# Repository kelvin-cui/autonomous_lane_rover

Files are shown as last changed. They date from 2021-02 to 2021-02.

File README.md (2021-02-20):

# autonomous lane following rover
152375054-496836404648972-4190929028758680099-n

Autonomous lane-following rover using openCV to identify and predict lane positions, and KP feedback loop for movement control, and ROS as a robotics framework to combine different modules together. The image processing was done on a Raspberry Pi 4B, which sends the appropriate motor commands to an Arduino Nano, which then sends the commands to stepper motors controlling a differential drive.

## objective
The lane-following rover was designed to follow a lane marked by duct tape, as a proof of concept for future projects. I wanted to create a project utilizing ROS and feedback control schemes, which I learned in class. OpenCV was something that I wanted to learn on my own, applying it for lane detection for this project. Putting these together, I wanted to create a robot that would follow a track with challenging features, such a chicanes and decreasing radius turns. 

rover

## software design:

### lane detection:
The lane detection was done utilizing OpenCV, in the camera.py module. When a ROS image is received, the module first converts it to an OpenCV image. The image is then masked to only detect a certain distance away from the rover, ignoring objects in the distant background. It then finds the canny edges, which are then grouped into lanes using hierarchical clustering, based on each points relative euclidian distance. Then, the cluster of points is fitted to a quadratic equation, which predicts the lane position near the center of the robot. It then finds the middle of the lane in terms of pixels as well as phi_avg, the angle the lanes are relative to the robot. 

Lane Detection:

*Left: The white lines are the predicted lanes, green are the left and right lane x locations, and the red line represents the middle of both lanes, as well as the slope of the lane. Right : The Canny Edges detected after the mask is applied*

### movement:
x_avg and phi_avg are then used in a KP feedback loop. x_avg is centred at 0, ranging from -320pixels to +320pixels (the camera has a resolution of 640 pixels across). Similarly, phi_avg is centred at 0, ranging from -90degrees to 90degrees. Both are normalized to -1/+1, and then used in a proportional feedback loop to regulate the values to zero. The forward velocity is fixed at 0.07m/s, while the rotational velocity is controlled by this feedback loop, with tunable gains on the x_error and phi_error. This can all be found in move.py. Once the rotational velocity is determined, it's then sent to motor.py, which takes the linear and rotational velocities and calculates the rotational speed of each motor.

Lane Following:

### ros and optimization:
The different modules communicate using the ROS framework. The original camera image is published to the image_raw topic, which is subscribed to by the camera.py node. The camera node publishes to the x_avg and phi_avg topics with Float64 values, which is subscribed to by the move.py node. The Move node then publishes Twist messages, including the linear and rotational velocities, which are subscribed to by the motor.py node. The motor.py node communicates the motor commands over serial to the Arduino. 

I made use of two external ros packages - the usb_cam test package in order to quickly publish images from the Pi Camera, and the web_video_server package to visualize the images for debugging.

The camera node requires the most computational time - as a result, it was optimized to have a maximum runtime of 0.06 seconds on the Pi4, allowing for a global rate of 10hz. 

## mechanical/electrical design:
The mechanical design of the rover went through multiple iterations of refinement. V1 was designed with DC motors in mind, but even with a gearbox, there was not fine enough control to accurately position the rover on the relatively small table surface.

roverv1

As a result, V2 used stepper motors, as well as a stand-alone Arduino Nano that communicated with the Raspberry Pi over serial to control the motors. However, this design used the default V1.3 Pi Camera, which had a minimum focus distance of 0.5m - too far for our use. Furthermore, the position of the drive motors at the rear increased the torque required to turn the robot, causing in slippage of the tires.

roverv2

The final design came with moving the differential drive tires to the middle, as well as moving the camera module to the top of the robot to get as clear of an image as possible. The camera was swapped for the wide angle module, and the microprocessors were moved to the top as they required the most interaction. This redesign also allowed the entire rover to be much more compact, utilizing the space given as effectively as possible. 

roverv3

The Arduino connects to two ULN2003 stepper driver modules, which are then connected to 28BYJ-48 Stepper Motors. The Raspberry Pi 4 is powered by an external 10000mAh battery bank capable of delivering 3A at 5V. The Arduino Nano is powered over the USB connection with the Raspberry Pi, while the stepper drivers have a separate 5V connection to the battery bank.

The layered design was heavily inspired by racing quadcopters, where carbon fiber plates would be layered on top of one another using standoffs. All parts were designed in Solidworks, and 3D printed using PETG.

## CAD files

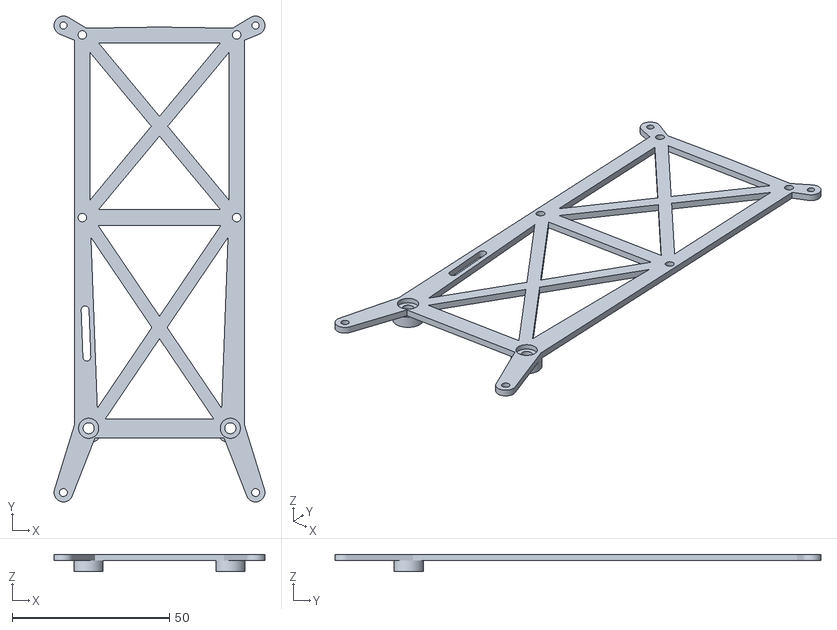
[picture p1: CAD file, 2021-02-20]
STL/board_mount_v3.STL
67.0 x 154.3 x 5.50

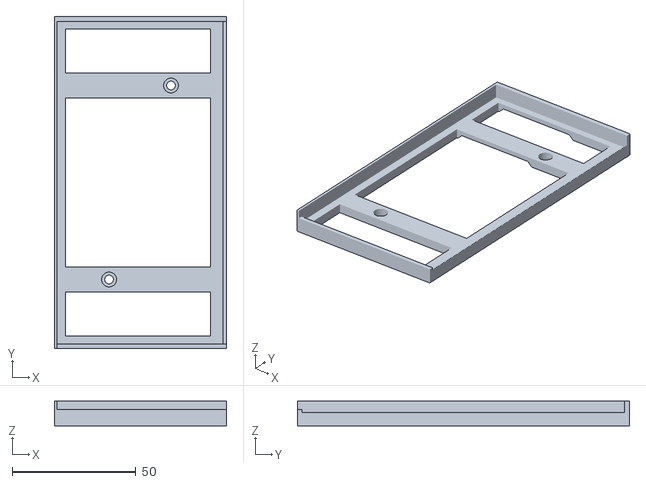
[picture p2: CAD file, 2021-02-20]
STL/batterymount_v3.STL
69.4 x 134.0 x 10.1

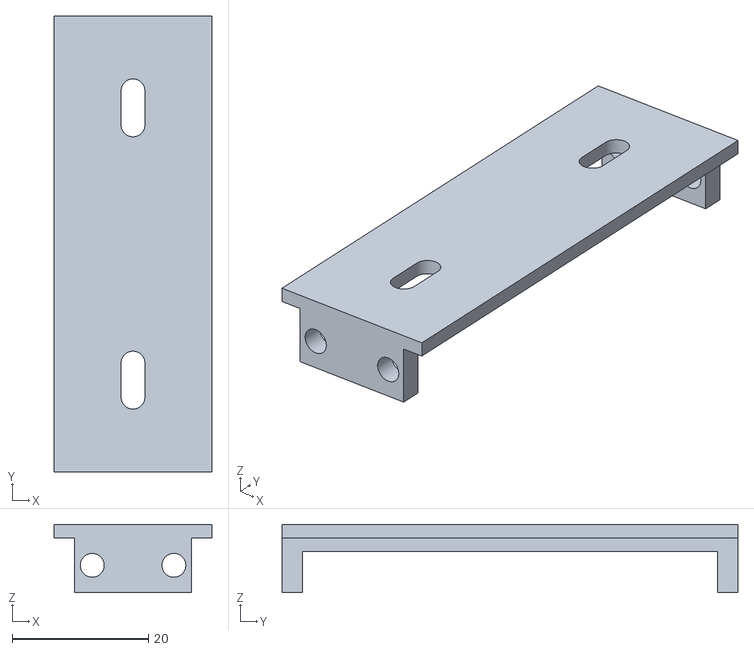
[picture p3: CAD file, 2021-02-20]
STL/castermount.STL
23.1 x 67.0 x 10.0

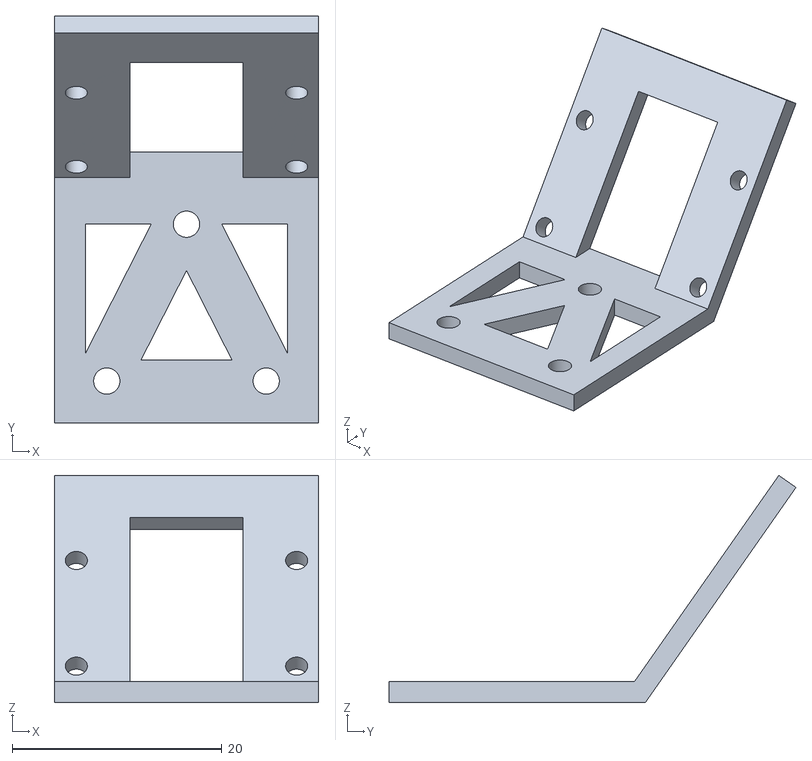
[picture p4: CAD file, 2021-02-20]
STL/camera_mount_v3.STL
25.2 x 38.8 x 21.7

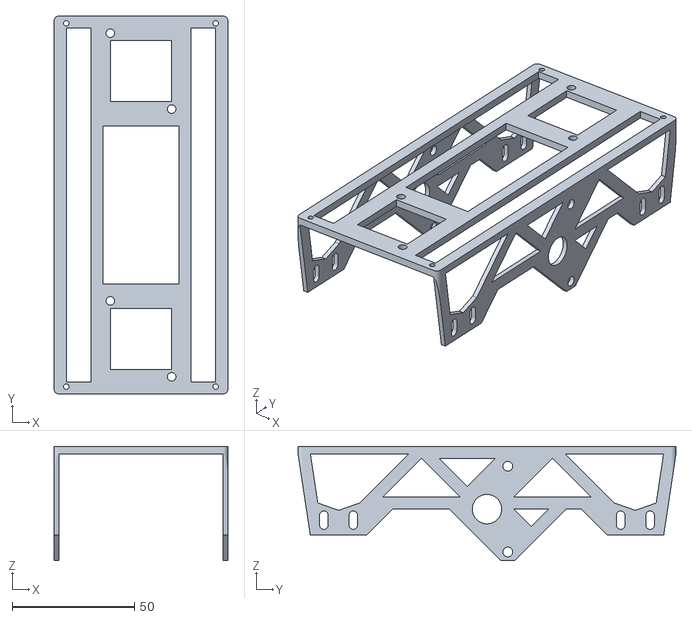
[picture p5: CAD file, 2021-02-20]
STL/roverbase_v3.STL
71.0 x 154.3 x 46.6

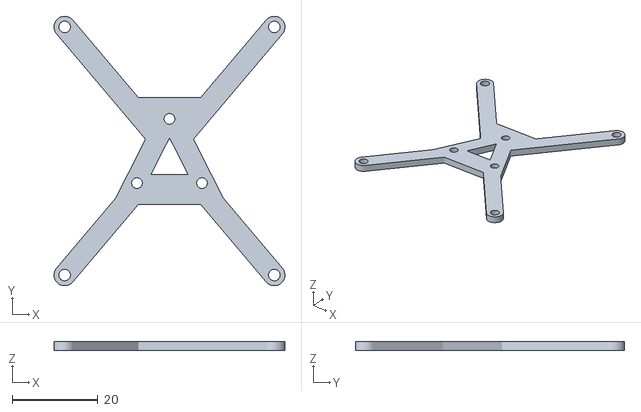
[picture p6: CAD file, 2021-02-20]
STL/camera_plate_v3.STL
54.0 x 63.0 x 2.00

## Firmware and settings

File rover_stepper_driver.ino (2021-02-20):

/* Rover Stepper Motor Control for use with ROS - Kelvin Cui */

#include <AccelStepper.h>

#define right_motorPin1  2      
#define right_motorPin2  3      
#define right_motorPin3  4     
#define right_motorPin4  5     

#define left_motorPin1 6
#define left_motorPin2 7
#define left_motorPin3 8
#define left_motorPin4 9



#define MotorInterfaceType 8

AccelStepper right_stepper = AccelStepper(MotorInterfaceType, right_motorPin1, right_motorPin3, right_motorPin2, right_motorPin4);
AccelStepper left_stepper = AccelStepper(MotorInterfaceType, left_motorPin1, left_motorPin3, left_motorPin2, left_motorPin4);

const byte numChars = 32;
char receivedChars[numChars];
char tempChars[numChars];
char msgChar[numChars] = {0};

float right_speed, right_cmd, left_speed, left_cmd;

boolean newData = false;
int sleeptimer;

void setup() {
  // Set the maximum steps per second:
  right_stepper.setMaxSpeed(1100);
  left_stepper.setMaxSpeed(1100);
  Serial.begin(9600);
  
  right_speed = 0;
  left_speed = 0;
  right_cmd = 0;
  left_cmd = 0;
  sleeptimer = 0;
}
void loop() {
  getData();
  if (newData == true) {
    sleeptimer = 0;
    right_stepper.enableOutputs();
    left_stepper.enableOutputs();
    strcpy(tempChars, receivedChars);
    parseData();
    newData = false;
  }

  //28byj is 4076 steps for 1 revolution - therefore 11.3 steps per degree or 648.7step/rad
  right_cmd = (right_speed * -648.7);
  left_cmd = (left_speed * 648.7);
  
  if (sleeptimer > 25000){
    //Serial.print("Sleeping | ");
    right_stepper.setSpeed(0);
    left_stepper.setSpeed(0);

    right_stepper.disableOutputs();
    left_stepper.disableOutputs();
  }

  else {
    right_stepper.setSpeed(right_cmd);
    left_stepper.setSpeed(left_cmd);

    sleeptimer += 1;
  }
  right_stepper.runSpeed();
  left_stepper.runSpeed();
  //Serial.println(sleeptimer);
}

void getData() {
  static boolean inprogress = false;
  static byte ndx = 0;
  char startMarker = '<';
  char endMarker = '>';
  char rc;

  while (Serial.available() > 0 && newData == false) {
    rc = Serial.read();

    if (inprogress == true) {
      if (rc != endMarker) {
        receivedChars[ndx] = rc;
        ndx += 1;
        if (ndx >= numChars) {
          ndx = numChars - 1;
        }
      }

      else{
        receivedChars[ndx] = '\0';
        inprogress = false;
        ndx = 0;
        newData = true;
      }
    }

    else if (rc == startMarker) {
      inprogress = true;
    }
  }
}

void parseData() {
  char * strtokndx;

  strtokndx = strtok(tempChars, ",");
  right_speed = atof(strtokndx);

  strtokndx = strtok(NULL, ",");
  left_speed = atof(strtokndx);
}

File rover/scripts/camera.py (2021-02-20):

#!/usr/bin/env python
import rospy
import RPi.GPIO as GPIO
import cv2
import numpy as np

from scipy.cluster.hierarchy import dendrogram, linkage, fcluster
from cv_bridge import CvBridge, CvBridgeError
from sensor_msgs.msg import Image
from std_msgs.msg import Float64


class images:
    def __init__(self):
        self.image_pub = rospy.Publisher('cv_stream', Image, queue_size=1)
        self.x_error_pub = rospy.Publisher('x_error', Float64, queue_size=3)
        self.phi_error_pub = rospy.Publisher('phi_error', Float64, queue_size=3)
        self.test_pub = rospy.Publisher('testing_stream', Image, queue_size=1)
        
        self.sub = rospy.Subscriber("usb_cam/image_raw", Image, self.imageprocessing)
        self.bridge = CvBridge()
        self.last_lanes = [-999, -999]
       
    #----Main CV Processing----#    
    def imageprocessing(self, msg, verbose = False, test = True):
        if verbose:
          starttime = rospy.get_time()
        try:
            cv_image = self.bridge.imgmsg_to_cv2(msg, "bgr8")
        except CvBridgeError as e:
            rospy.loginfo("cv conversion error: " + str(e))
            
        cv_image_rotated = cv2.rotate(cv_image, cv2.ROTATE_180)
        cv_canny = self.canny(cv_image_rotated)
        cv_masked = self.addmask(cv_canny)
        
        lane_edges = self.find_edges(cv_masked)
        [cv_lines, x_error, phi_error] = self.curved_lines(cv_image_rotated, lane_edges,True)
        cv_final = cv2.addWeighted(cv_lines, 0.8, cv_image_rotated, 1, 1)
        
        try:
            self.image_pub.publish(self.bridge.cv2_to_imgmsg(cv_final, "bgr8"))
            self.x_error_pub.publish(x_error)
            self.phi_error_pub.publish(phi_error)
            if test:
              self.test_pub.publish(self.bridge.cv2_to_imgmsg(cv_masked, "mono8")) #mono8
            if verbose:
              print("Image Processing took %f seconds" %(rospy.get_time() - starttime))

        except CvBridgeError as e:
            rospy.loginfo("publish error: " + str(e))
            
    #---Sub Functions---#
    def canny(self, frame):
        blurred_frame = cv2.GaussianBlur(frame,(5, 5), 0)
        return cv2.Canny(blurred_frame, 125, 200)
        
    def addmask(self, frame):
        h, w = frame.shape[:2]
        triangle = np.array([[(int(10), int(6*h/7)), (int(w-10), int(6*h/7)), (int(w-10), int(5*h/7)), (int(10), int(5*h/7))]])
        mask1 = np.zeros_like(frame)
        cv2.fillPoly(mask1, triangle, 255)
        frame = cv2.bitwise_and(frame, mask1)
        return frame 
             
    def find_edges(self, frame):
        line_frame = np.zeros_like(frame)
        edges = []
        
        np_frame = np.array(frame)
        
        (x, y) = np.nonzero(np_frame)
        temp_edges = zip(y,x)
       
        if temp_edges != []:    
            cluster = linkage(temp_edges, method = 'single', metric = 'euclidean')
            group = fcluster(cluster, 5, criterion='distance')
            edges =[ [[],[]] for idx in range( max(group))]
        
            for i in range(0, len(temp_edges)):
                edges[group[i] - 1][0] += [temp_edges[i][0]] #x array
                edges[group[i] - 1][1] += [temp_edges[i][1]] #y array

        return edges
        
    
    def curved_lines(self, frame, edges, plot=False):
        line_frame = np.zeros_like(frame)
        h, w = frame.shape[:2]
        x_avg = -1
        phi_avg = -1
        lanes = []     
        lane1 = [-1,-1,0]
        lane2 = [-1,-1,0]

        for idx in range(0, len(edges)):
          coeff = np.polyfit(edges[idx][1],edges[idx][0], 2) #fit quadratic equation to group of points to estimate lane curvature
          existing_lane = False
          
          if len(edges[idx][0]) > 50: #lane lines will have at least 50 points in worst case - anything shorter will be ignored
            if plot:
              y = np.linspace(h/2, h, 5)
              x = np.polyval(coeff, y)
              points = (np.asarray([x, y]).T).astype(np.int32) 
              cv2.polylines(line_frame, [points], False, (255,255,255), thickness = 3)
  
            x_line = coeff[0]*(4/3)*h**2 + coeff[1]*(4/3)*h + coeff[2] #find x intercept at "center" of rover
            phi = (2*coeff[0]*(6*h/7) + coeff[1]) #find slope at 1/7th height up frame to anticipate curvature from first derivative of polynomial

            for i in lanes: #group lines with similar x intercepts together
              if (x_line) - 100 <= i[0]/i[2] <= (x_line + 100):
                i[0] += x_line 
                i[1] += phi
                i[2] += 1
                existing_lane = True
                break
              
            if existing_lane == False: #if the lane x_intercept isn't close to any other existing lane in lanes array
              lanes += [[x_line, phi, 1]]

        for i in lanes:
          if (i[2] > 1): #lanes will have at least 2 lines combined from above, anything less than that can be ignored
            cv2.line(line_frame, (self.within_frame(i[0]/i[2], w), h), (self.within_frame(i[0]/i[2], w), 9*h/10), (0,255,0), 3)
          
            if i[2] > lane1[2]:
                lane2 = lane1
                lane1 = [i[0]/i[2], i[1]/i[2], i[2]]
                
            elif i[2] > lane2[2]:
                lane2 = [i[0]/i[2], i[1]/i[2], i[2]]
        
        if lane1[0] != -1 and lane2[0] != -1:
          x_avg = (lane1[0] + lane2[0])/ 2 #take average of right and left lines
          phi_avg = -1*np.arctan((lane1[1] + lane2[1])/ 2)*180/np.pi #find angle in rads of slope
          cv2.line(line_frame, (self.within_frame(x_avg, w), h), (self.within_frame((x_avg - ((lane1[1] + lane2[1])/ 2)*h/5), w), 4*h/5), (0,0,255), 3)
          self.last_lanes = [lane1[0], lane2[0]]
          
        cv2.putText(line_frame, ("x error :" + str(x_avg - 320)), (50,50), cv2.FONT_HERSHEY_SIMPLEX, 1, (0,255,0), 2, cv2.LINE_AA, False)
        cv2.putText(line_frame, ("phi error :" + str(phi_avg)), (50,100), cv2.FONT_HERSHEY_SIMPLEX, 1, (0,255,0), 2, cv2.LINE_AA, False)

        return [line_frame, x_avg, phi_avg]
    
    #--Helper Function--#
    def within_frame(self, index, w):
      return int(min(w, max(0, index)))
                
     
def main(args=None):
    rospy.init_node('cv', anonymous=True)
    im = images()
    try:
        rospy.spin()
    except KeyboardInterrupt:
        print("stopping")
    

if __name__ == '__main__':
    main()
